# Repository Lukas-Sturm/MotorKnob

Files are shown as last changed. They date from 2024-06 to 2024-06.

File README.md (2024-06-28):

# MotorKnob - Firmware

A very simple haptic device. Inspired by [Scott Bezek's Smart Motor Knob](https://github.com/scottbez1/smartknob) and [Karlitos/Binaris](https://store.binaris.io).

It uses my fork of [haptic-bldc-lib by VIPQualityPost](https://github.com/VIPQualityPost/haptic-bldc-lib).  
It can be interfaced with using I2C.

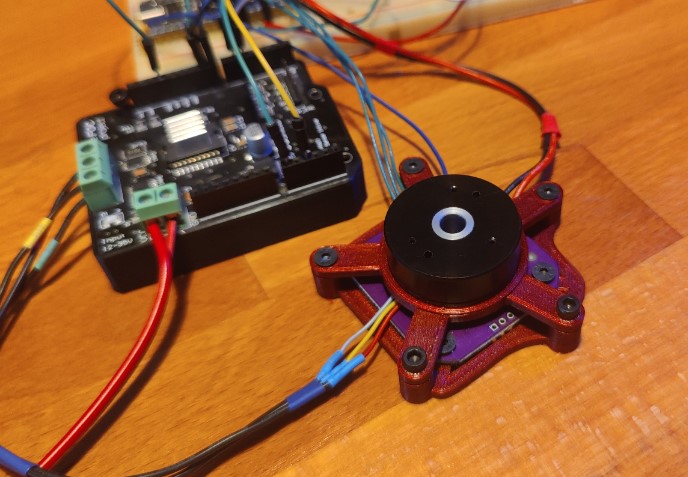
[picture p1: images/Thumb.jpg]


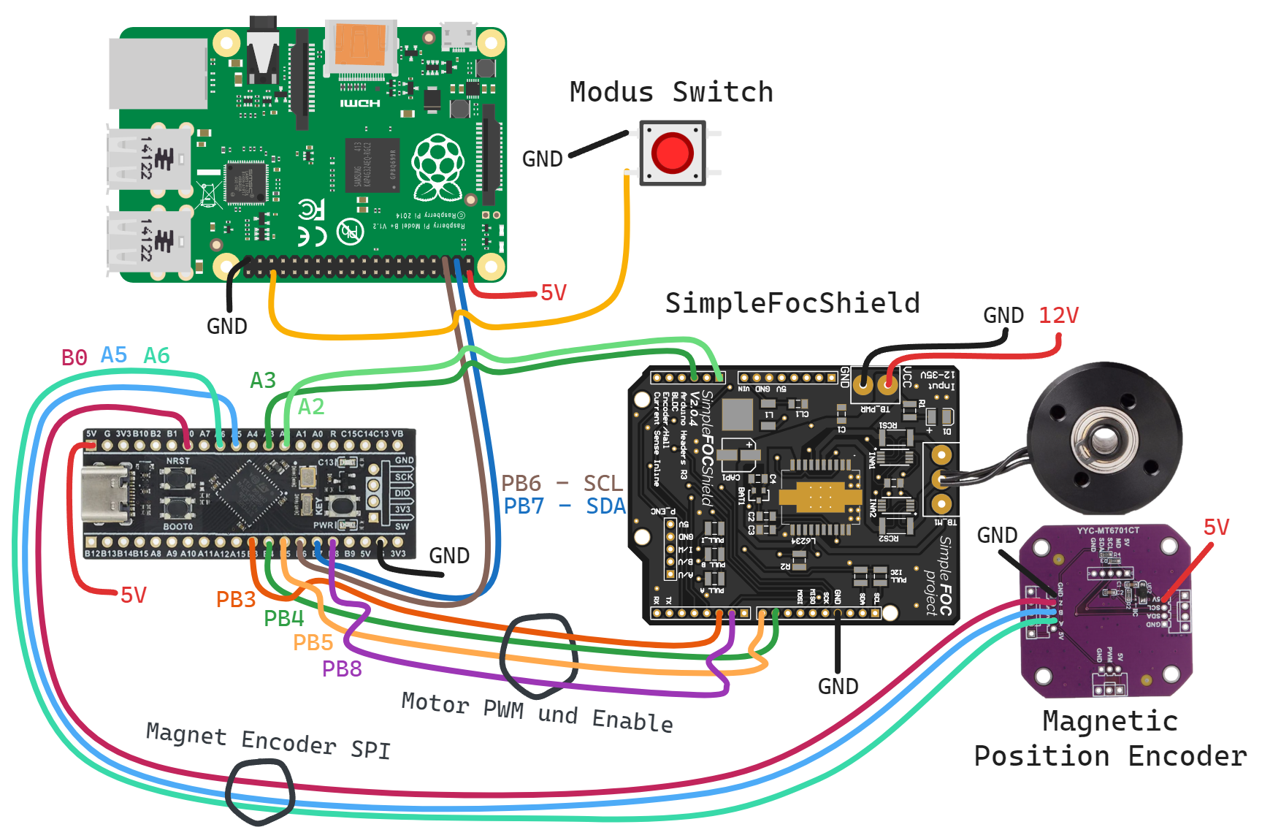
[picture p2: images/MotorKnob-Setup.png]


## Hardware
This uses a [special gimbal motor](https://www.sparkfun.com/products/20441).  
And a simple MT6701 Encoder (the big ones).  
In combination with a [SimpleFocShield](https://docs.simplefoc.com/arduino_simplefoc_shield_showcase).  
Everything running on a STM32F4.  

_STLs_ for a simple mount are included.  
Also checkout the Onshape Document for the [Motor Mount](https://cad.onshape.com/documents/7e04387006899651ea17d00d/w/a87f37efcacd94681ec261e1/e/0a7188be34b13700e3c3eeff) and the very basic [Shield Holder](https://cad.onshape.com/documents/3ccac3d901ce4e169d3a0e37/w/05fb2bf43415ca03ddd7f8aa/e/4bedb51f26a17385ea4008f9), feel free to adapt them to your needs.

## Driver
There is also a compatible [Linux Driver](https://github.com/Lukas-Sturm/MotorKnob-Driver) plus [Yocto Layer](https://github.com/Lukas-Sturm/meta-motorknob) available.  
Plus [Demo Application](https://github.com/Lukas-Sturm/MotorKnob-Demo) using it.

## Protocol
`communication.h` contains all the i2c/SMBus logic.  
I used a form of SMBus, it basically reads and writes words (2 bytes) per command, because this is supposed to interact with Linux a Driver.  

#### Reads
_First Byte_: Address Register   
_Second Byte_: Lower Data Byte  
_Third Byte_:  Upper Data Byte  

> adheres to SMBus standard for reading a word

#### Writes  
needs the address MSB set to 1  
position can't be written  

_e.g_:  
0b10000001 (0x81) __writes__ _end position_  
0x81 0x10 0x00 -> Sets __end position__ to 16.

> adheres to SMBus standard for writing (except the extra write bit)

### Registers
- `0x00` start position
- `0x01` end position
- `0x02` detent count
- `0x03` position

Bit 8 is reserved and indicates a Write command.

### Why not i2c read/write bit?
SMBus protocol always starts by sending a write with the register it wants to read/write. Then it either sends more data or sends a empty read package. That's why I need to set a write bit in the initial write command for the address. ¯\\_(ツ)_/¯ atleast that's how I got it running communicationg with Linux host.

## Notes
- This is very basic
- Currentsense is disabled (just stopped working with my setup)

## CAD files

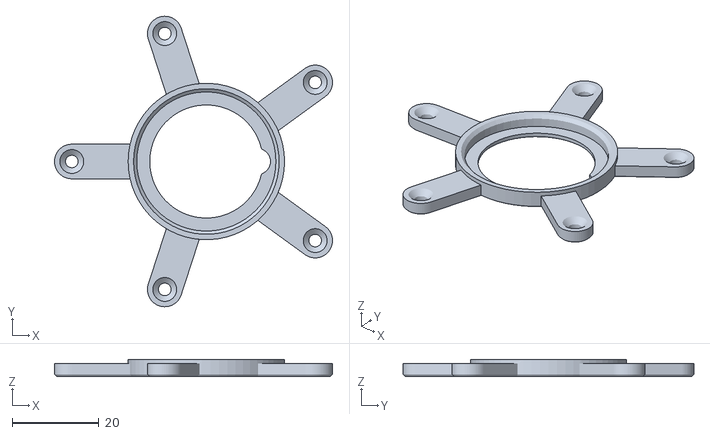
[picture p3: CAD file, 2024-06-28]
STLs/Motor-Holder.stl
64.2 x 67.1 x 3.95

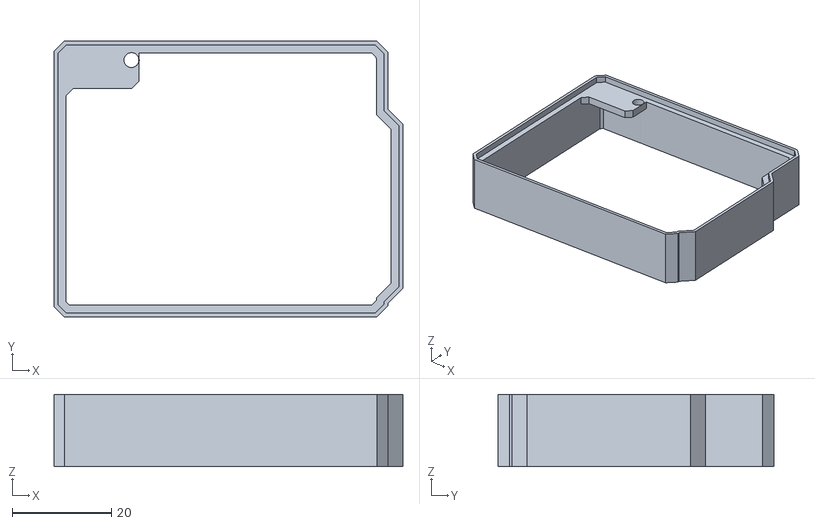
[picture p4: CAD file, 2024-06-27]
STLs/Shield-Holder.stl
70.4 x 55.6 x 14.6

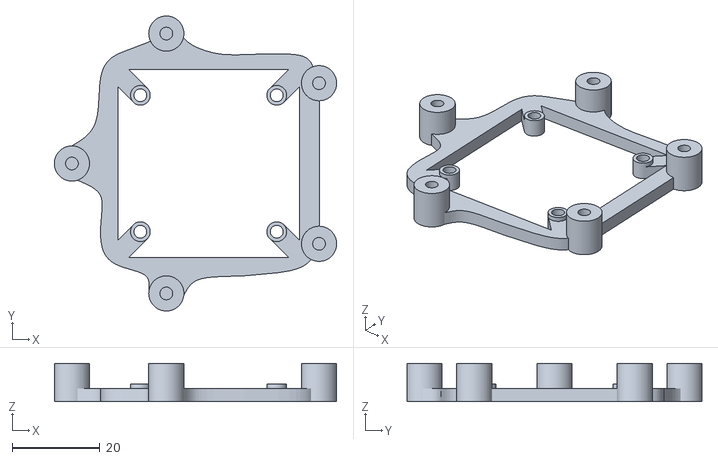
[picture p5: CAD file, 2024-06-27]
STLs/Encoder-Holder.stl
64.2 x 67.0 x 8.70

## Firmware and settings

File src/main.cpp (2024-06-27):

#include <Arduino.h>
#include <SPI.h>
#include <Wire.h>
#include <SimpleFOC.h>
#include <SimpleFOCDrivers.h>
#include <encoders/mt6701/MagneticSensorMT6701SSI.h>
#include <haptic.h>

#include "communication.h"
#include "motor.h"
#include "profiles.h"

#define MODE_BUTTON PA4
#define ROTARY_ENCODER_SSI_nCS PB0

// Main HapticInterface used to drive the motor and haptic feedback
HapticInterface haptic(&motor); // motor exported from motor.h

void UserHapticEventCallback(HapticEvt event, float currentAngle, uint16_t currentPos) {
      Serial.print("Event: ");
      Serial.print(event);
      Serial.print(" Angle: ");
      Serial.print(currentAngle);
      Serial.print(" Pos: ");
      Serial.println(currentPos);
}

DetentProfile defaultProfile = {
  .mode = HapticMode::REGULAR, // not used by library
  .start_pos = 80,
  .end_pos = 160,
  .detent_count = 80,
  .vernier = 0, // only multiplies detent_count by vernier and changes position counting
  .kxForce = false // not used by library
};

void setup() {
  Serial.begin(115200);
  _delay(1000); // wait for serial monitor to open

  Serial.println("Starting motor...");
  // SimpleFOCDebug::enable(&Serial);

  setup_simple_foc();
  haptic.setEventCallback(UserHapticEventCallback);
  haptic.haptic_state.load_profile(defaultProfile);
  haptic.init();

  setup_i2c(
    0x55,
    {
      .write_start_pos = [](uint16_t pos) -> void {
        defaultProfile.start_pos = pos;
        haptic.haptic_state.load_profile(defaultProfile);
        Serial.print("Wrote: start pos ");
        Serial.println(pos);
      },
      .write_end_pos = [](uint16_t pos) {
        defaultProfile.end_pos = pos;
        haptic.haptic_state.load_profile(defaultProfile);
        Serial.print("Wrote: end pos ");
        Serial.println(pos);
      },
      .write_detents = [](uint16_t detents) {
        defaultProfile.detent_count = detents;
        haptic.haptic_state.load_profile(defaultProfile);
        Serial.print("Wrote: detents ");
        Serial.println(detents);
      }
    },
    {
      .get_pos_func = []() -> uint16_t {
        return haptic.haptic_state.current_pos;
      },
      .get_start_pos_func = []() -> uint16_t {
        Serial.print("Read: start pos ");
        Serial.println(haptic.haptic_state.detent_profile.start_pos);
        return haptic.haptic_state.detent_profile.start_pos;
      },
      .get_end_pos_func = []() -> uint16_t {
        Serial.print("Read: end pos ");
        Serial.println(haptic.haptic_state.detent_profile.end_pos);
        return haptic.haptic_state.detent_profile.end_pos;
      },
      .get_detents_func = []() -> uint16_t {
        Serial.print("Read: detents ");
        Serial.println(haptic.haptic_state.detent_profile.detent_count);
        return haptic.haptic_state.detent_profile.detent_count;
      }
    }
  );
}

void loop() {
  // Runs haptic loop
  haptic.haptic_loop();
}

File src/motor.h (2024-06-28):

#pragma once

#include <Arduino.h>
#include <SPI.h>
#include <SimpleFOC.h>
#include <SimpleFOCDrivers.h>
#include <encoders/mt6701/MagneticSensorMT6701SSI.h>
#include <haptic.h>

#define ROTARY_ENCODER_SSI_nCS PB0

MagneticSensorMT6701SSI sensor(ROTARY_ENCODER_SSI_nCS);

//  BLDCMotor(int pp, (optional R, KV))
//  - pp  - pole pair number
//  - R   - phase resistance value - optional
//  - KV  - motor KV rating [rpm/V] - optional
// BLDCMotor motor = BLDCMotor(7, 3.6, 300);
BLDCMotor motor(7, 3.6);

InlineCurrentSense current_sense = InlineCurrentSense(0.01f, 50.0f, PA2, PA3);

BLDCDriver3PWM driver(PB3, PB4, PB8, PB5);

void setup_simple_foc() {
  sensor.init();

  // power supply voltage [V]
  driver.voltage_power_supply = 12;
  // Max DC voltage allowed - default voltage_power_supply
  driver.voltage_limit = 7;
  driver.init();

  // current_sense.linkDriver(&driver);
  // motor.linkCurrentSense(&current_sense);
  // current_sense.init();

  motor.linkSensor(&sensor);
  motor.linkDriver(&driver);
  motor.current_limit = 0.6;
  // motor.velocity_limit = 10;

  // overriden anyways
  motor.torque_controller = TorqueControlType::voltage;
  // motor.controller = MotionControlType::torque;

  // controller configuration based on the control type 
  motor.PID_velocity.P = 0.1;
  motor.PID_velocity.I = 3.0;
  motor.PID_velocity.D = 0.001;
  motor.LPF_velocity.Tf = 0.03;

  // angle loop controller
  motor.P_angle.P = 15;
  motor.P_angle.I = 2;
  motor.P_angle.D = 0.001;

  // initialize motor
  motor.init();

  // pre tested values for this exact setup
  // motor.sensor_direction = Direction::CW;
  // motor.zero_electric_angle = 5.3;

  // align sensor and start FOC
  // can be skipped, but currently mount is not super rigid 
  motor.initFOC();
}

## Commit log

2024-06-27 initial release
    [Encoder-Holder.stl, Motor-Holder.stl, Shield-Holder.stl]
2024-06-28 add wiring diagram, update holder stl
    [Motor-Holder.stl]
